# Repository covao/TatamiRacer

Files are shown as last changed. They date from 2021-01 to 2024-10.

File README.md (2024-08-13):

[Japanese](https://github.com/covao/TatamiRacer/blob/master/README_JP.md) / [English](https://github.com/covao/TatamiRacer/blob/master/README.md)  

TatamiRacerLogo
### ver 2.0      
TatamiRacer is a tiny autonomous driving car based on the ["TAMIYA MINI 4WD" kit](https://www.tamiya.com/english/mini4wd/m4item/m4item.htm). It can operate within the space of a single ["Tatami"](https://en.wikipedia.org/wiki/Tatami) mat, approximately 1.8m x 0.9m. The car uses ["Donkey Car"](http://docs.donkeycar.com/) software for deep learning and self-driving control. Interestingly, the Japanese word "Tatami" also brings to mind convolution operations in neural networks.

### YouTube  
- TatamiRacer 

(https://www.youtube.com/watch?v=b-pkVy8e3DA)  

- TatamiRacer at Maker Faire Tokyo 2022  

(https://www.youtube.com/watch?v=s3ll8Y1OPn8)  

# Release History

### [ver 1.0](https://github.com/covao/TatamiRacer/tree/1.0) 2023-05-28
### [ver 2.0](https://github.com/covao/TatamiRacer)
- Renewed 3D Parts
- Reduced mobile battery size and weight
- Supports installation of Raspberry Pi Zero 2

# Bills of Materials(BOM)
| Parts Name | Remarks |Minimum Configuration|Recommend Configuration|Amazon-JP|Amazon-US|
|:---|:---|:---:|:---:|:---:|:---:|
| Raspberry Pi Zero2 W ||+|| [Link](https://www.amazon.co.jp/dp/B09LH5SBPS/) | [Link](https://www.amazon.com/dp/B09LH5SBPS) |
| Raspberry Pi 4 |Select 2,4 or 8GB RAM||+| [Link](https://www.amazon.co.jp/dp/B09GRVDPCX/) | [Link](https://www.amazon.com/dp/B07TC2BK1X) |
| Raspberry Pi Camera Module  | v1.3:OV5647(Omnivision) or v2.1:IMX219Pq3(SONY)|+|+| [v1.3](https://www.amazon.co.jp/dp/B073RCXGQS/), [v2.1](https://www.amazon.co.jp/dp/B01F1SWTZE)| [v1.3](https://www.amazon.com/dp/B07QNSJ32M/),  [v2.1](https://www.amazon.com/dp/B01ER2SKFS)|
| Micro SD Card | 16GB or more|+|+| [e.g. SanDisk](https://www.amazon.co.jp/dp/B0CH2WM7QY/) | [e.g. SanDisk](https://www.amazon.com/dp//B08J4HJ98L) |
| Mobile Battery | Size:53x85x9.0mm Voltage:5V Current:Up to 2.1A |+|+|[Meisei C0303](https://www.amazon.co.jp/dp/B07Q5M3CLQ/) | [Atom Tech Super Slim Power Bank](https://www.amazon.com/dp/B07JZCZSH9/) |
| Motor Driver Module| For DC Motor/H-Bridge|+|+| [L298N ](https://www.amazon.co.jp/dp/B083DT2DMV/) |[L298N ](https://www.amazon.com/dp/B07Y1QJZK3/) |
| Pin Headder | Male 90deg / For Motor Dirver|+|+| [Link](https://www.amazon.co.jp/dp/B00V4V703O/) |[Link](https://www.amazon.com/dp/B0979568B3/) |
| 130 DC Motor | Low Speed (<8000 RPM) and Low Current(<500mA)|+|+|[TAMIYA](https://www.amazon.co.jp/dp/B005AFBLIA/),[uxcell](https://www.amazon.co.jp/dp/B07CWLWRYJ/) | [uxcell](https://www.amazon.com/dp/B01ERLPVJW) |
| Micro Servo |TowerPro SG90(0.1sec/60deg)|+|+| [Link](https://www.amazon.co.jp/dp/B016FKJJ8M/) | [Link](https://www.amazon.com/dp/B07MLR1498/) |
| TAMIYA Mini 4WD Kit |VZ Chassis and Your Favorite Body. Select Gear Rate 3.5:1 or 5:1 (Recommend 5:1 Gear )|+|+| [Elephant with 5:1 gear](https://www.amazon.co.jp/dp/B08VX3W3Q6/), [TOYOTA Yaris with 3.5:1 Gear](https://www.amazon.co.jp/dp/B08C5FM9HM/), [Honda e with 3.5.1 Gear](https://www.amazon.co.jp/dp/B08HK7HWCM/), [Dual Ridge Jr](https://www.amazon.co.jp/dp/B088FK3NC2/) | [Elephant with 5:1 gear](https://www.amazon.com/dp/B08VX3W3Q6/), [TOYOTA Yaris with 3.5:1 Gear](https://www.amazon.com/dp/B08C5FM9HM/), [Honda e with 3.5.1 Gear](https://www.amazon.com/dp/B08HK7HWCM/), [Dual Ridge Jr](https://www.amazon.com/dp/B088FK3NC2/) |
|TAMIYA Gear Set |If you change gear rate (e.g. 5:1)|||[15516](https://www.amazon.co.jp/dp/B0043RN7W4/)|[15516](https://www.amazon.com/dp/B0043RN7W4/)|
| TAMIYA Mini 4WD Roller parts | Need Spacer and M2x10 screws|+|+| [15381](https://www.amazon.co.jp/dp/B001E40PXI/), [95391](https://www.amazon.co.jp/dp/B07F8RLJBQ/),[15435](https://www.amazon.co.jp/dp/B005GJCC9C/)|[15435](https://www.amazon.com/dp/B005GJCC9C/) | 
| M2x15 or M2x16 mm bolt | For front wheel shaft |+|+| [15508](https://www.amazon.co.jp/dp/B01MXVKDOM/),  [15233](https://www.amazon.co.jp/dp/B001VZE9MS/)| [Link](https://www.amazon.com/dp/B07YS5ZSZH/) |
| TAMIYA MINI4WD 72mm Shaft | For Extended Rear Shaft|+|+| [Link](https://www.amazon.co.jp/dp/B003GALRS0/) | [Link](https://www.amazon.com/dp/B002CAO2IC/) |
| Jumper Cable | Female connector to Female connector 10cm|+|+| [Link](https://www.amazon.co.jp/dp/B07MR1SVVR/) | [Link](https://www.amazon.com/dp/B0742RS6YL) |
| Type-C USB Cable(L Headder) | Short cable 15-20cm ||+| [e.g. aceyoon](https://www.amazon.co.jp/dp/B0B4JQ41SW/)| [e.g. aceyoon](https://www.amazon.com/dp/B096VYVR17/) |
| Gamepad | USB or Bluetooth | |+| [F710](https://www.amazon.co.jp/dp/B00CDG7994/), [PS4 Compatible Gamepad](https://www.amazon.co.jp/dp/B0C4NW3G8J/)  | [F710](https://www.amazon.com/dp/B0041RR0TW/), [PS4 Compatible Gamepad](https://www.amazon.com/dp/B0C4NW3G8J/) |
||  || |  |  |
| Approximate cost (without Raspberry Pi and micro SD card) |  |6,000 yen |10,000 yen |  |  |

# 3D Printed Parts

## Assembly
See [3D Viewer](3d/tatamiracer_assembly.stl)  
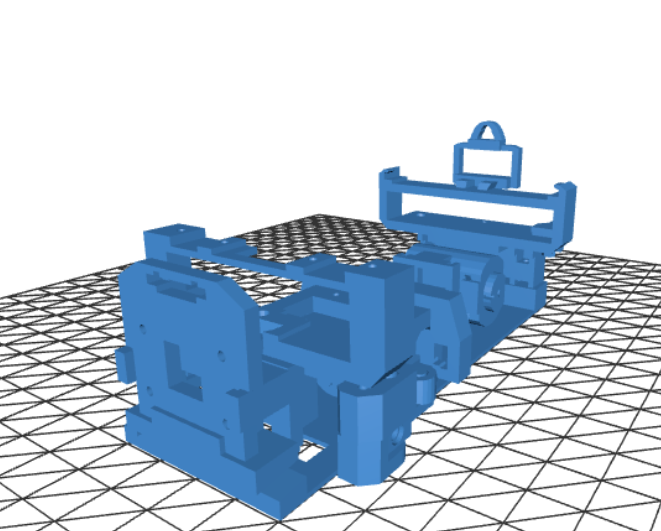
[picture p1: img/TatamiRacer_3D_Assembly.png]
  
  
## Kit for 3D print
See [3D Viewer](3d/tatamiracer_kit.stl)  
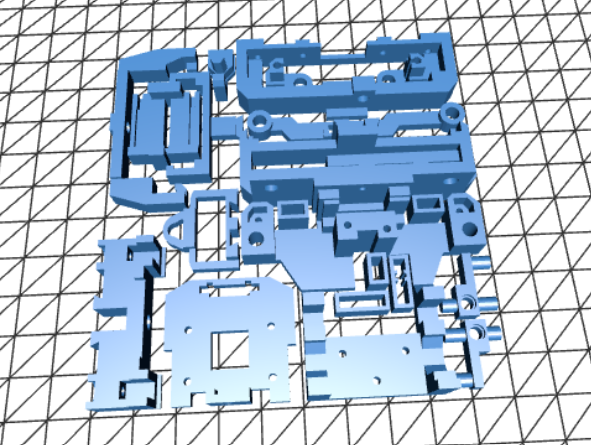
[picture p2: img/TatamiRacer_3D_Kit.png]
  
  
# Circuit Diagram
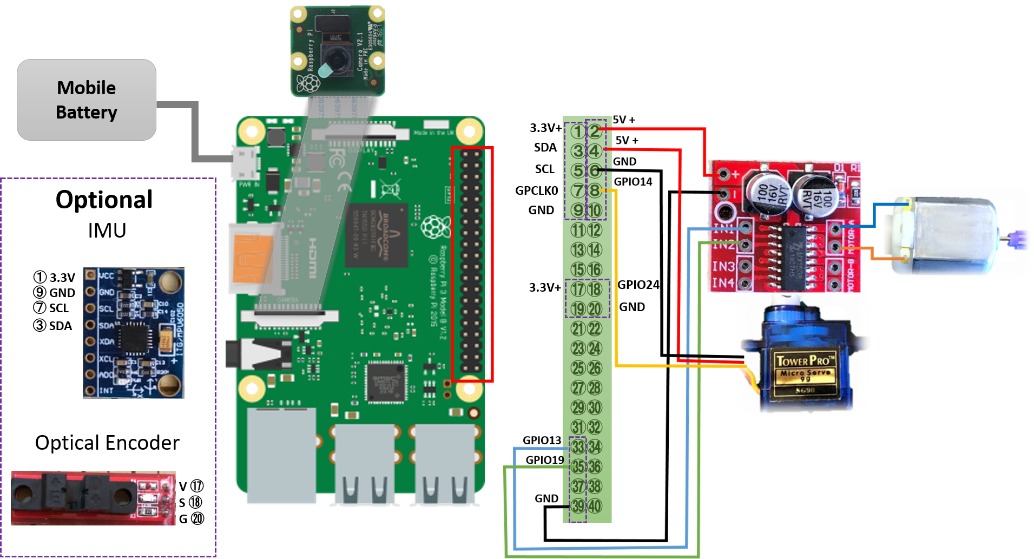
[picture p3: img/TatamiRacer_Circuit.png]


# Body
Various type of Mini-4WD body can be attaced .e.g. [Amazon JP](https://www.amazon.co.jp/s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), [Amazon US](https://www.amazon.com/s?k=tamiya+1%2F32+mini4wd&ref=nb_sb_noss)  
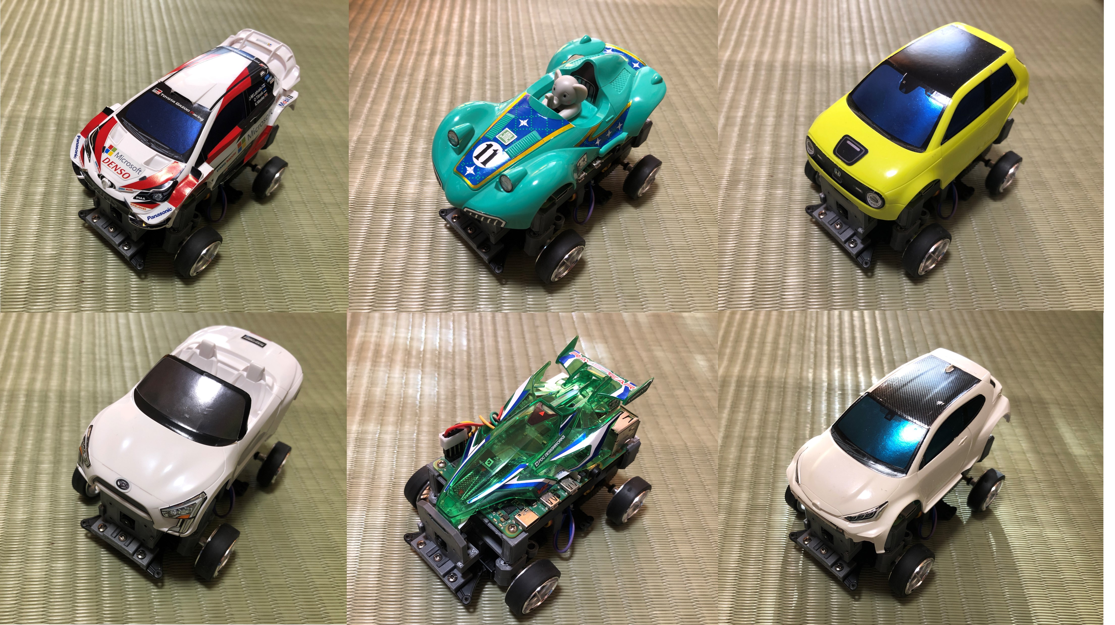
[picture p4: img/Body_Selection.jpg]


# Tatami-Circuit Cource
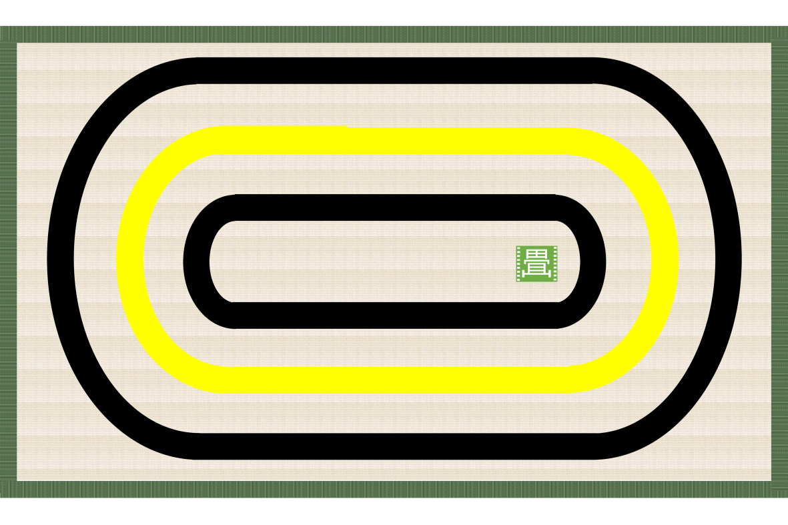
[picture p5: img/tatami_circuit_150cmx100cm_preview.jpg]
  

## Image data for printed fabric 
Fabric print service available  
- [Tatami-Circuit 150cmx100cm 200dpi](img/tatami_circuit_150cmx100cm_200dpi.jpg)  
- [Tatami-Circuit 110cmx100cm 200dpi](img/tatami_circuit_110cmx100cm_200dpi.jpg)  

# [TatamiRacer Assembly Instructions](doc/Assembly_Instructions.md)
See [TatamiRacer Assembly Instructions](doc/Assembly_Instructions.md)  
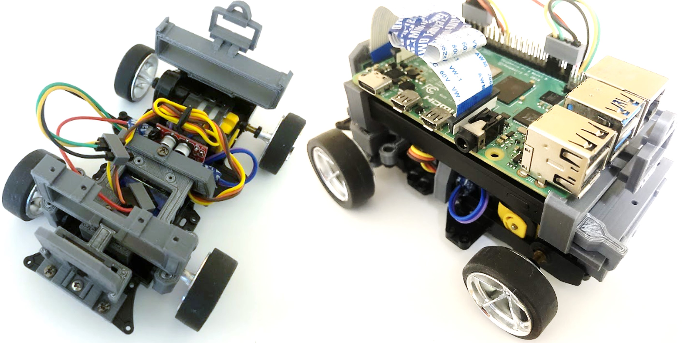
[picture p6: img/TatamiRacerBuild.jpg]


# [How to Setup Software](doc/HowToSetupSoftware.md) 
See [How To Setup Software](doc/HowToSetupSoftware.md)  
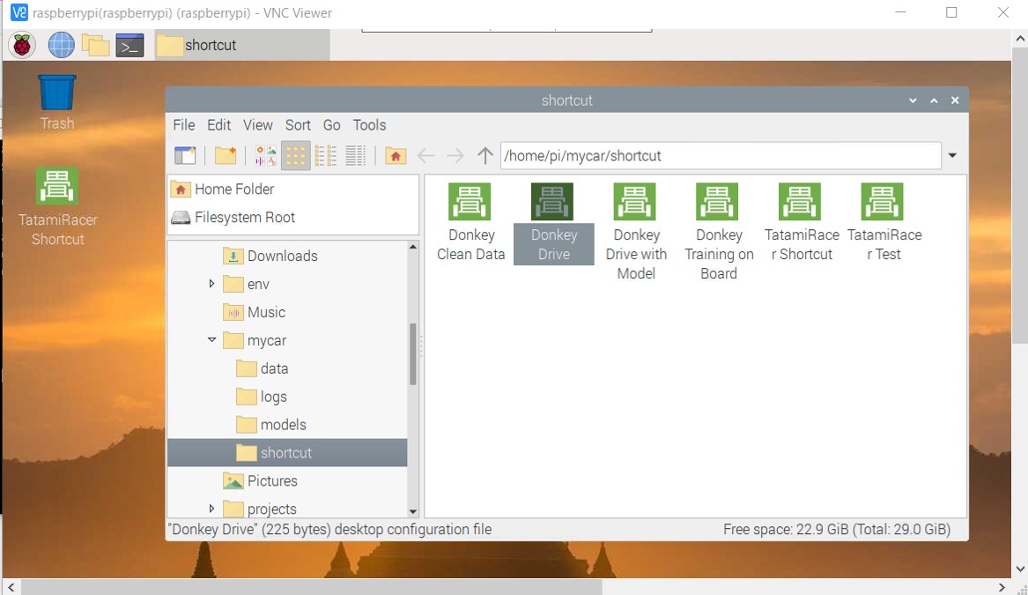
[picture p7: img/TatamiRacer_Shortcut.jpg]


#  [How to Calibrate TatamiRacer](doc/HowToCalibrateTatamiRacer.md)  
See [How to Calibrate TatamiRacer](doc/HowToCalibrateTatamiRacer.md)  
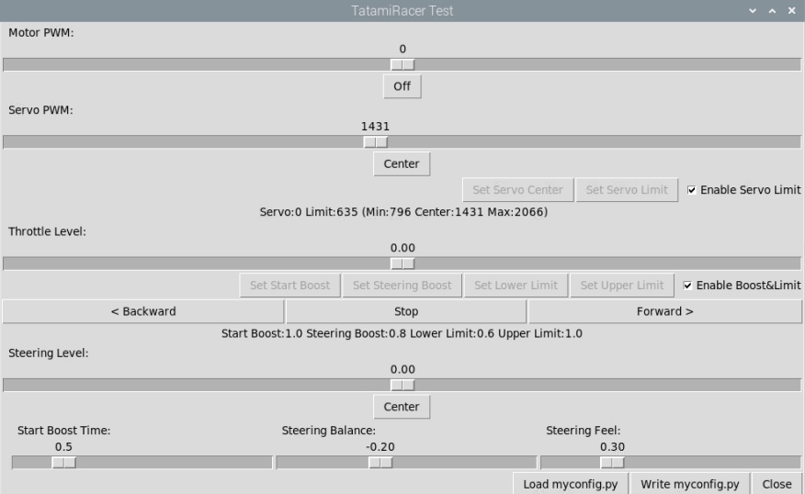
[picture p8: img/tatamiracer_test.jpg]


# [How to Get Driving](doc/HowToGetDriving.md)
See [How to Get Driving](doc/HowToGetDriving.md)  
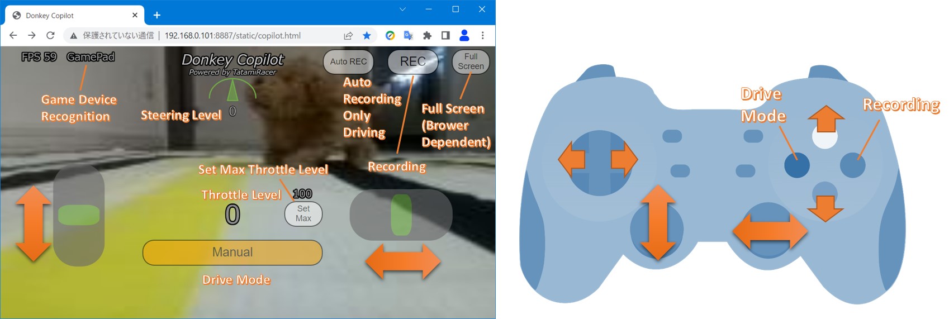
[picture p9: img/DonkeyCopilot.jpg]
  

Click to see the UI operation screen  
[Donkey Copilot Broweser Demo](https://covao.github.io/DonkeyCopilot/copilot.html?demo)

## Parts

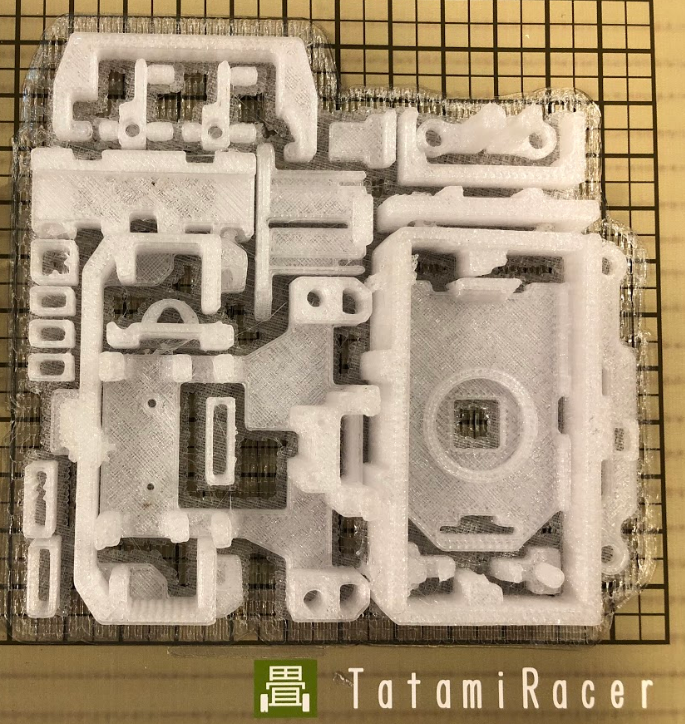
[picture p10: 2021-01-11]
img/printed_parts.png

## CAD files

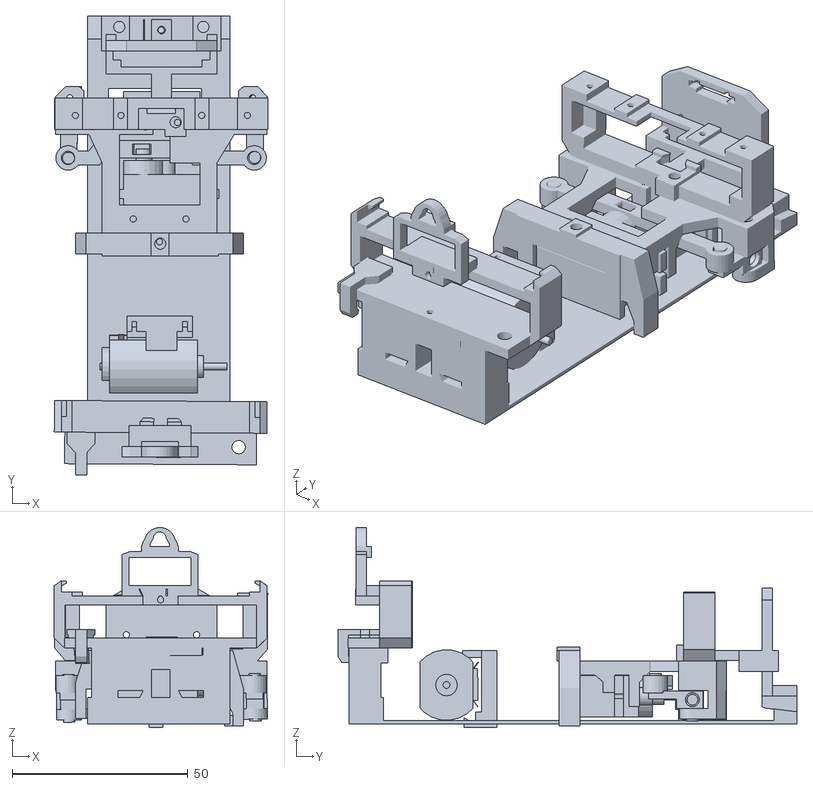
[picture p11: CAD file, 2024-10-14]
3d/tatamiracer_assembly.stl
60.8 x 130.7 x 57.0

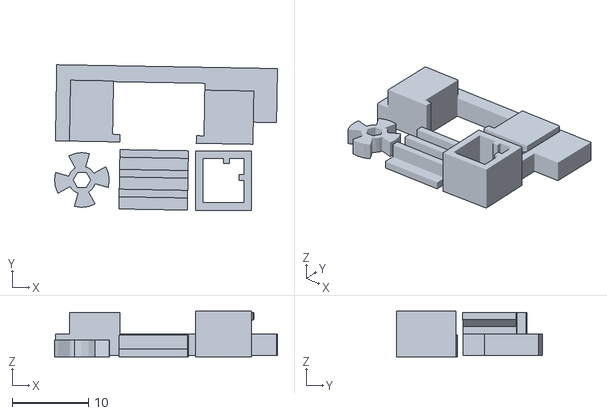
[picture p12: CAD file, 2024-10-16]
3d/tatamiracer_encoder_kit.stl
29.3 x 19.1 x 6.00

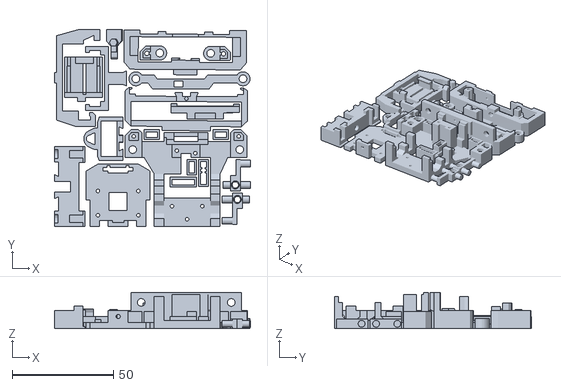
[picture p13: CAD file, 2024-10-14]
3d/tatamiracer_kit.stl
97.0 x 97.3 x 18.0

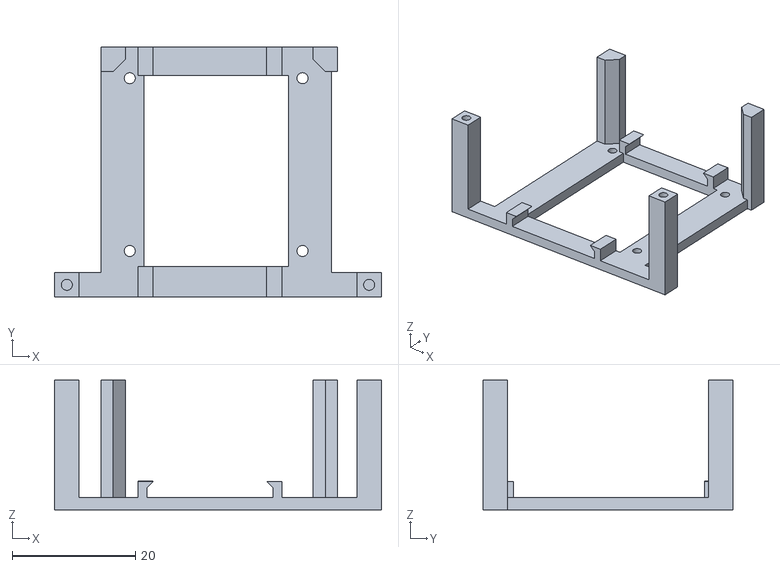
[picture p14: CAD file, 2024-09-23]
3d/lidar_mount_kit.stl
53.0 x 40.6 x 21.0

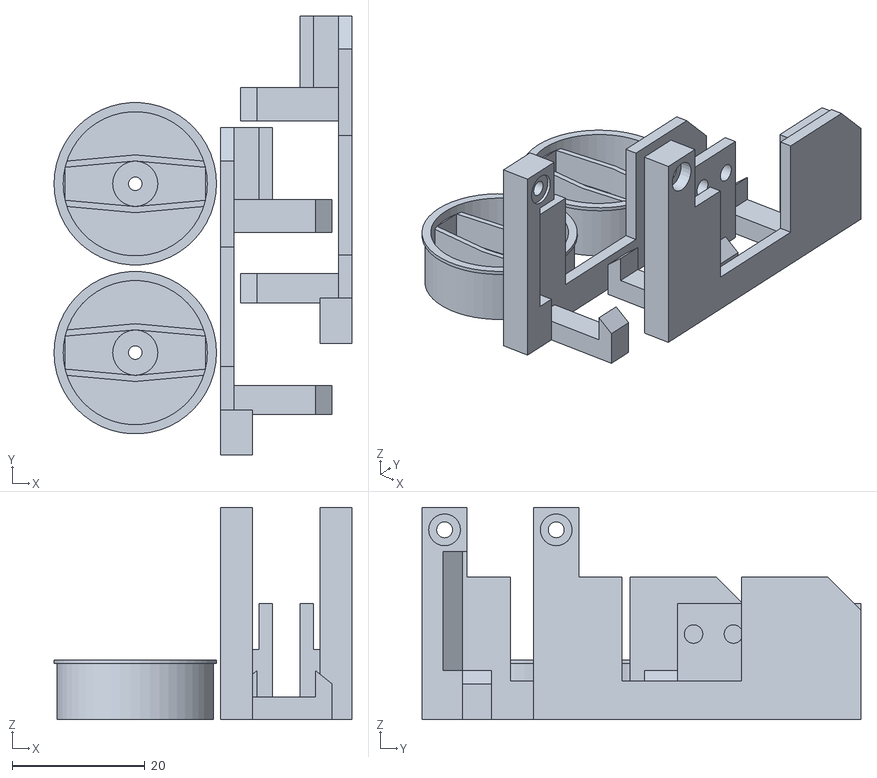
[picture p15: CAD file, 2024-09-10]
3d/differential_wheel_kit.stl
44.9 x 66.1 x 32.0

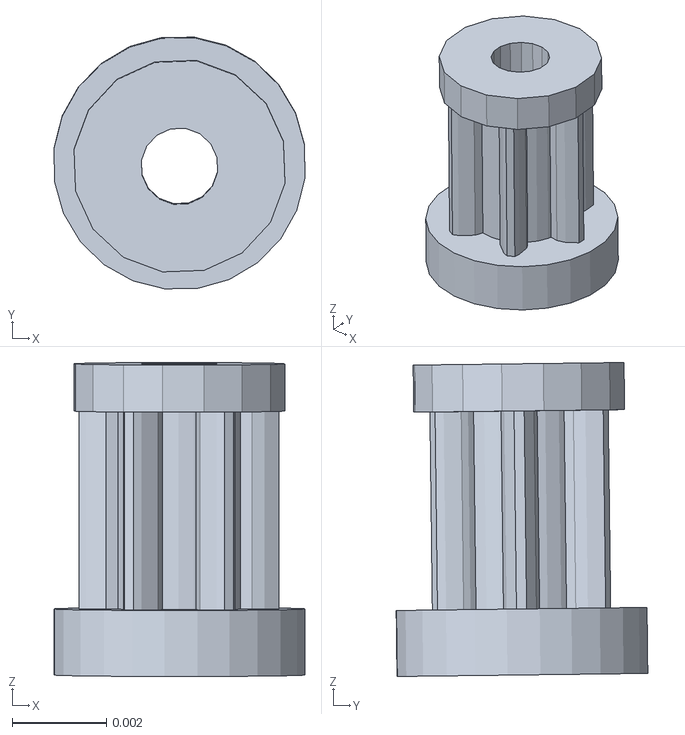
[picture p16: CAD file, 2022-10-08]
3d/pinion_gear_6t.stl
0.00532 x 0.00534 x 0.00666

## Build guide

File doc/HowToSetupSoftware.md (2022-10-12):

[Japanese(Google Translate)](https://github-com.translate.goog/covao/TatamiRacer/blob/master/doc/HowToSetupSoftware.md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)  

# How To Setup Software

TatamiRacer can use DonkeyCar software.  
This page describes about installing DonkeyCar software and custumizing TatamiRacer.  

# Install Raspberry Pi OS using Raspberry Pi Imager
1. Download "Raspberry Pi Imager" from [Raspberry Pi official site](https://www.raspberrypi.org/software/). 
2. Install "Raspberry Pi Imager".
3. Start "Raspberry Pi imager".
4. Downlowd Raspbian-OS file from the following site.    
For TatamiRacer it is recommended to install the desktop version.  
Stable Raspbian version for DonkeyCar 
https://downloads.raspberrypi.org/raspios_armhf/images/raspios_armhf-2021-05-28/  
	2021-05-07-raspios-buster-armhf.zip     
 See note of Raspbian Bullseye issue of Donkey Car.
 [Flash Operating System](https://docs.donkeycar.com/guide/robot_sbc/setup_raspberry_pi/#step-1-flash-operating-system)

5. If you press advanced configration button, you can set WIFI, host name, SSH, user name and password, local setting.
6. Write Raspbian OS to your micro SD card.
7. Un plugging and re-inserting micro SD card.
8. Check the SD card drive. Boot files are appeared if OS image was flashed successfuly.

# Setup the WiFi for Raspberry Pi
Internet connection on Raspberry Pi is required before installation.
## - Method 1: WiFi setting in the Raspberry Pi Desktop (Monitor and keyboard for Raspberry pi are required.)
1. Insert micro SD card into Raspi.
2. Plug USB power supply of Raspi.
3. Login Raspberry Pi Desktop
4. Set Wifi configuration from Raspberry pi Desktop  
 See [Wireless connectivity in the Raspberry Pi Desktop](https://bwww.raspberrypi.org/documentation/configuration/wireless/desktop.md)
## - Method 2: WiFi setting by boot configuration file (Remote access is available without Raspi monitor and keyboard.) 
1. Create wpa_supplicant.conf in the top of SD card then edit ssid and password by texteditor  
 Please see ["Setting up a Raspberry Pi headless"](https://docs.donkeycar.com/guide/robot_sbc/setup_raspberry_pi/)
2. Create ssh file (empty file) in the top of SD card to enable SSH.  
 Please see ["SSH (Secure Shell)>3. Enable SSH on a headless Raspberry Pi"](https://www.raspberrypi.org/documentation/remote-access/ssh/)
3. Insert micro SD card into Raspi.
4. Plug USB power supply of Raspi and wait few minutes.
5. Launch command prompt and enter following command.  
 Check network connection between host pc and raspberry pi.  
~~~
 ping raspberrypi
 
~~~
OR
~~~
 ping raspberrypi.local
 
~~~

6. Launch ssh by following command.  
~~~
ssh-keygen -R raspberrypi
ssh pi@raspberrypi

~~~
If <code>"The authenticity of host 'raspberrypi... Are you sure you want to continue connecting (yes/no)?"</code> is appeared, enter yes.  

7. Enter password. Initial Password:<code>raspberry</code>

# Setup VNC
Remote desktop environment is useful to access Raspberry pi from host pc.  
1. You can install VNC with the following command.  
(You can enter the command from remote ssh or Raspberry pi desktop ternminal.)  
~~~
yes | sudo apt-get update
yes | sudo apt install realvnc-vnc-server realvnc-vnc-viewer
yes | sudo raspi-config nonint do_vnc 0

~~~
2. Set screen resolution
Select "Display Options-> Resolution" (At least 1280 x 720 recommended.)
~~~
sudo raspi-config

~~~
3. Select exit and reboot.  

4. Installation on the host PC is also requreired.  
See ["VNC (Virtual Network Computing)"](https://www.raspberrypi.org/documentation/remote-access/vnc/).  

# Launch Raspberry Pi Desktop
If you have VNC installed, you can use Remote Desktop.
1. Start Raspberry Pi Desktop.  
2. Launch Terminal window.

# Install Donkey Car Application for Raspberry Pi
## Method 1: Install by Shell Script 
1. First execute the following command.  
~~~
yes | sudo apt-get update
yes | sudo apt-get upgrade

~~~
*Press q when you see the following message.
<code>if webkit2gtk (2.31.1-1) experimental; urgency=medium ...</code>

2. The following command will install the latest Donkey Car application and create default "mycar" application.
~~~
wget "https://raw.githubusercontent.com/covao/TatamiRacer/master/raspi/install/install_donkey_raspi.sh" -O "install_donkey_raspi.sh"
sh -x install_donkey_raspi.sh

~~~
The shell script is here. [install_donkey_raspi.sh](https://raw.githubusercontent.com/covao/TatamiRacer/master/raspi/install/install_donkey_raspi.sh)

## Method 2: Install Manually Step by Step
See following procedure.
- [Get Your Raspberry Pi Working Step6 -Step12 ](https://docs.donkeycar.com/guide/robot_sbc/setup_raspberry_pi/#step-6-update-and-upgrade)
- [Create your car application](https://docs.donkeycar.com/guide/create_application/)

# Setup TatamiRacer by Shell Script 
The following command will replace 'manage.py' and 'config.py' and add 'tatamiracer_test.py' for TatamiRacer.  
In addition it will create the shortcut into desktop.  
~~~
wget "https://raw.githubusercontent.com/covao/TatamiRacer/master/raspi/install/setup_tatamiracer.sh" -O "setup_tatamiracer.sh"
sh -x setup_tatamiracer.sh

~~~
The shell script is here. [setup_tatamiracer.sh](https://raw.githubusercontent.com/covao/TatamiRacer/master/raspi/install/setup_tatamiracer.sh)



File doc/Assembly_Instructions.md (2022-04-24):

[Japanese(Google Translate)](https://github-com.translate.goog/covao/TatamiRacer/blob/master/doc/Assembly_Instructions.md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)  

# TatamiRacer Assembly Instructions 
### All Parts 
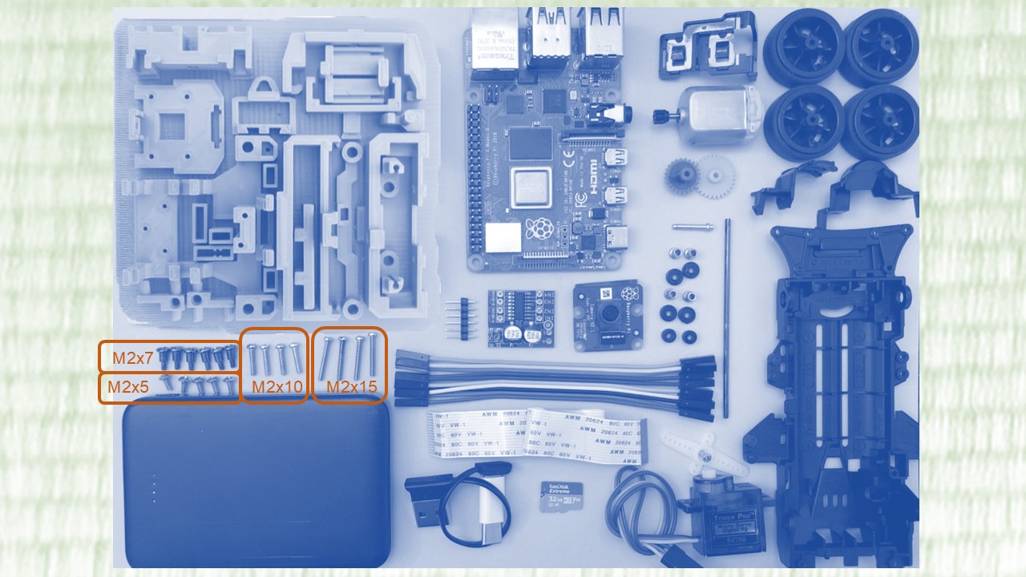
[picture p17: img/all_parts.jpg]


### Step 1. Assembling Front Wheel Parts
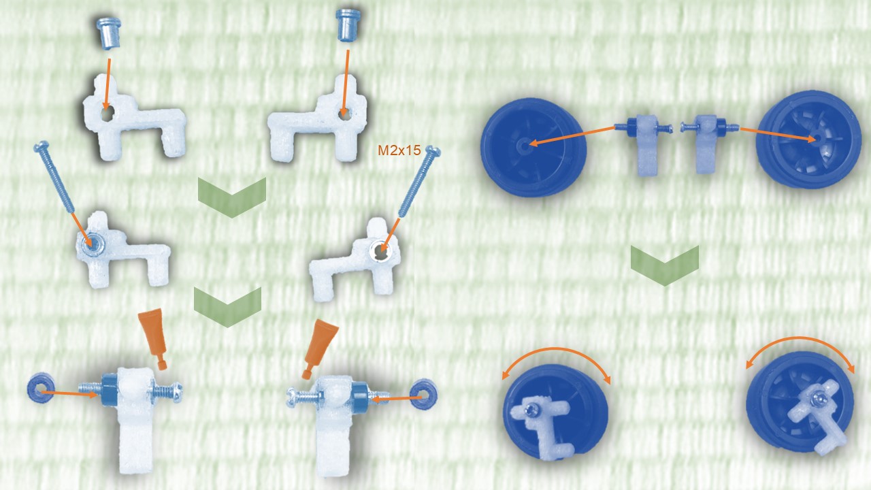
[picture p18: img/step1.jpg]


### Step 2. Assembling Front Steering Unit
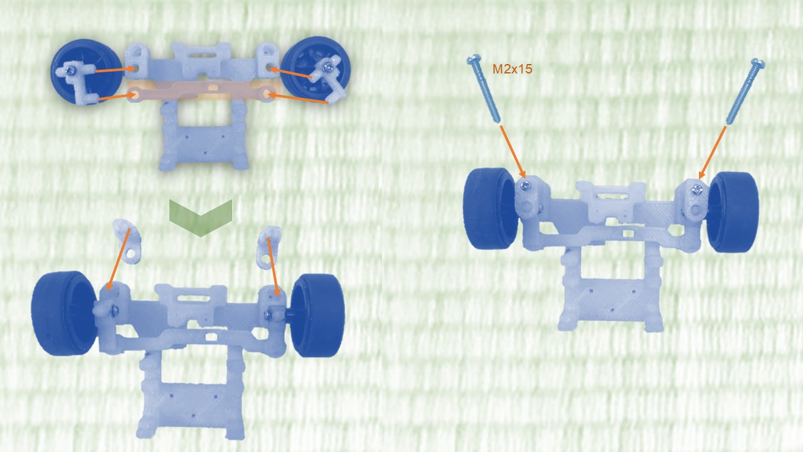
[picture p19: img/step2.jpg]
 

### Step 3. Assembling Servo Motor
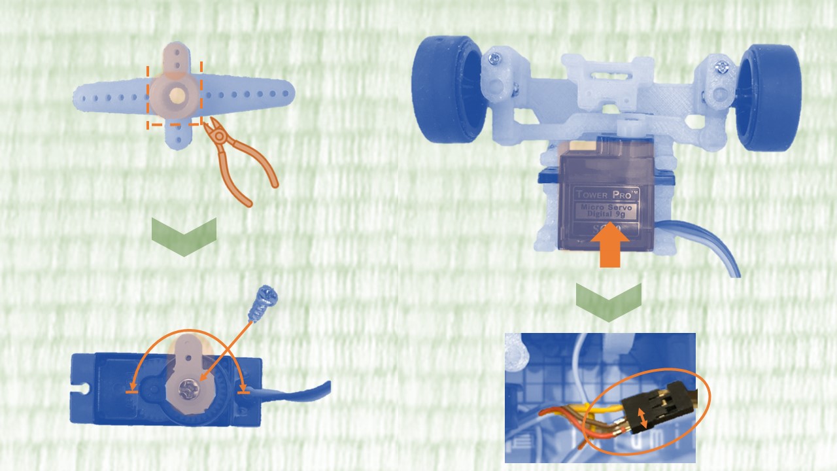
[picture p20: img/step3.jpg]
 

### Step 4. Mounting Front Steering Unit 
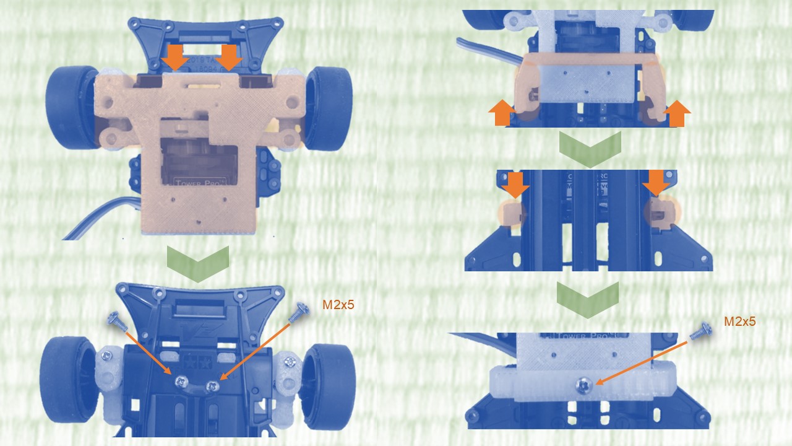
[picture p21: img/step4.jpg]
 

### Step 5. Assembling Rear Wheel Drive Unit
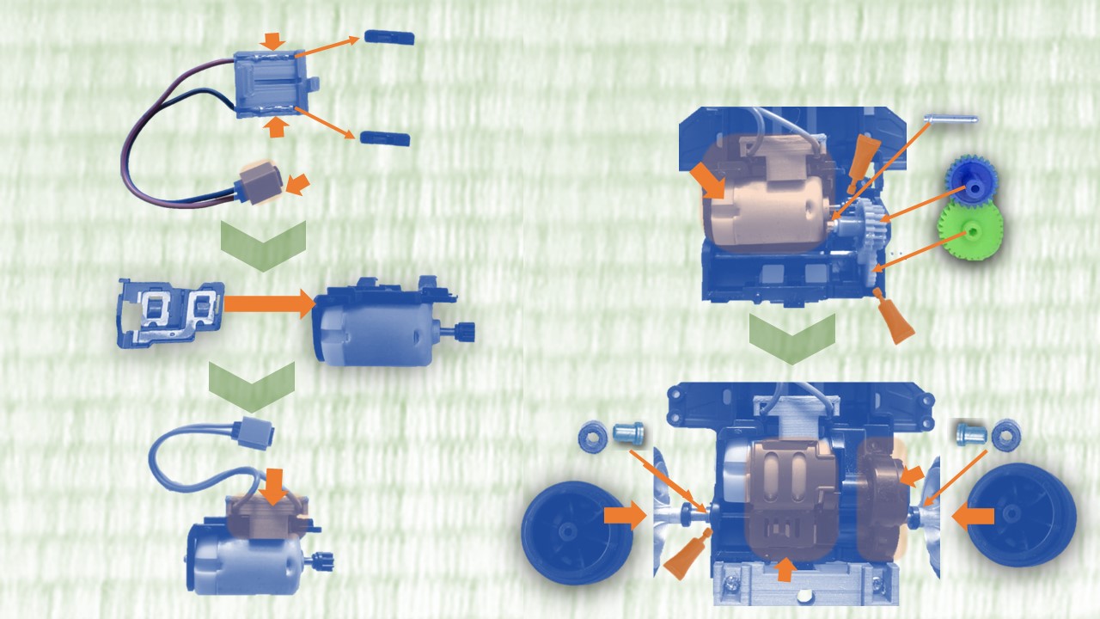
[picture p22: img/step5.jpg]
 

### Step 6. Fixing Mount Parts
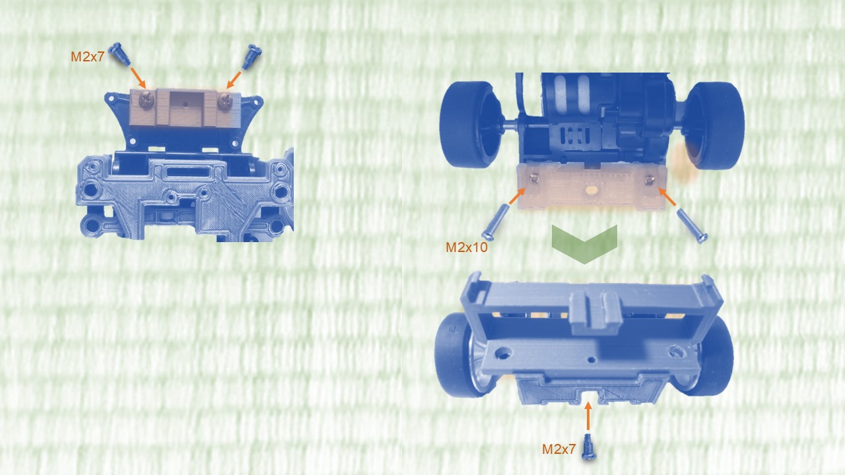
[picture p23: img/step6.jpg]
 

### Step 7. Assembling Camera Module 
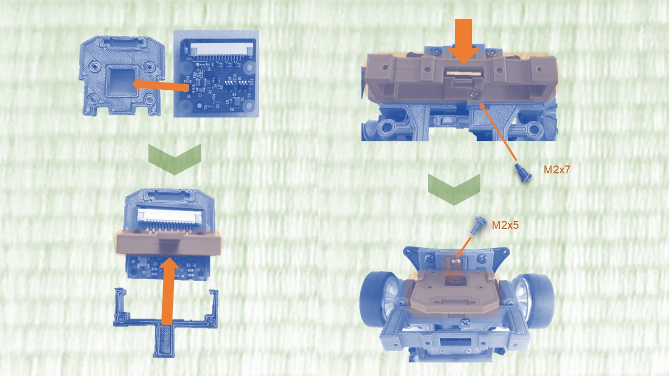
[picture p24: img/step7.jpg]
 

### Step 8. Making Motor Driver and Harness 
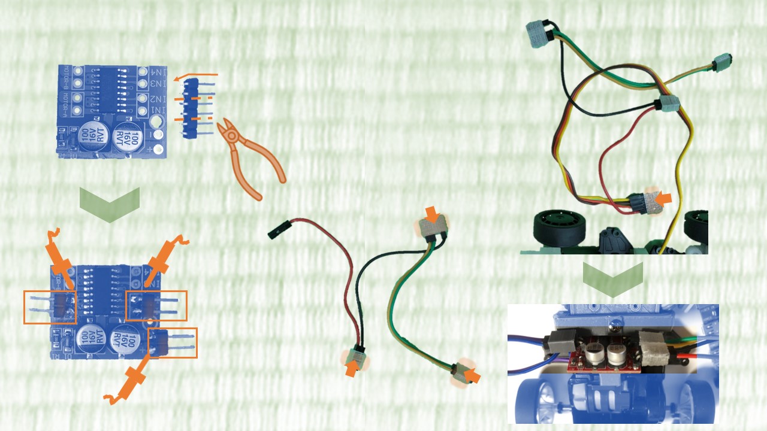
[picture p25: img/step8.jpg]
 

### Step 9. Attaching Raspberry PI Board and Battery
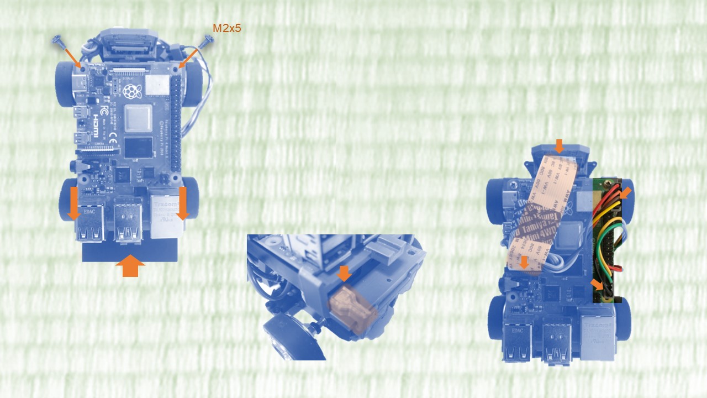
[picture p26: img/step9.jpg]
 

### Step 10. Attaching the body
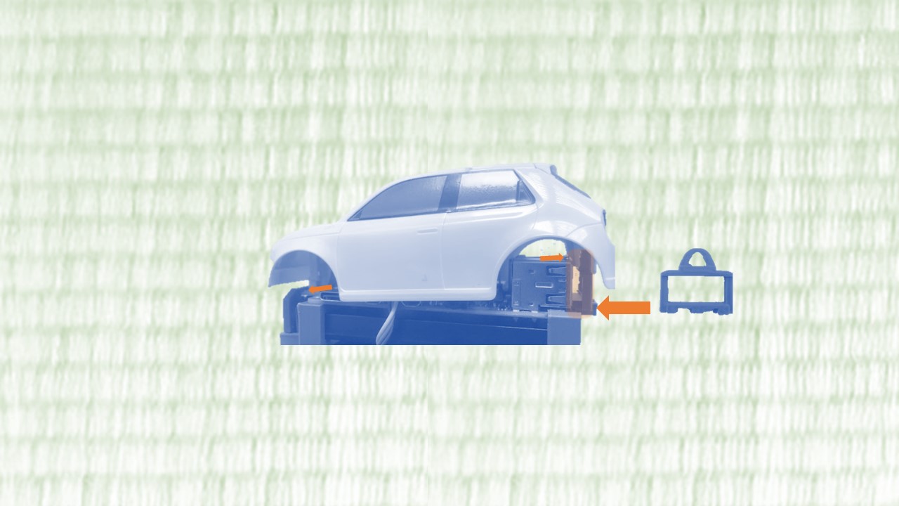
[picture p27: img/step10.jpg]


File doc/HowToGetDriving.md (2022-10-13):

[Japanese(Google Translate)](https://github-com.translate.goog/covao/TatamiRacer/blob/master/doc/HowToGetDriving.md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)
# How To Get Driving
TatamiRacer can be operated remotely with the web browser.  
This article is how to drive with a DonkeyCar web controller.  
See below for more information.
- [DonkeyCar > Drive your car](https://docs.donkeycar.com/guide/get_driving/)

## Start DonkeyCar Application
### Method 1: Desktop Shortcut 
1. Start "Donky Drive" or "Donky Drive with Model  


### Method 2: Command from terminal
1. Enter following command from terminal.
~~~
cd ~/mycar
python manage.py drive
~~~

## Web Controller
### Method 1: Donkey Copilot (Web controller suitable for smartphone)  

Please see https://github.com/covao/DonkeyCopilot

### [Demo Link](https://covao.github.io/DonkeyCopilot/copilot.html?demo)  

### Method 2: DonkeyCar web Controller  
2. Start the Web browser from the host PC or smart phone and enter following URL.
~~~
http://raspberrypi:8887/drive
~~~

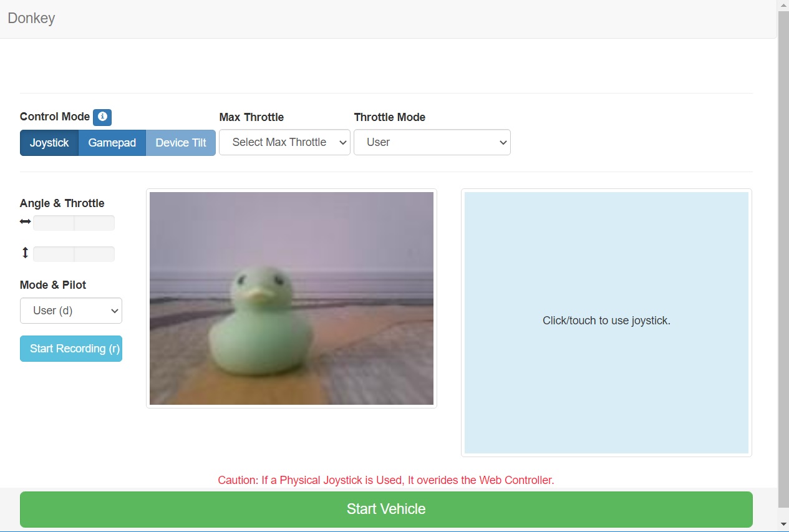
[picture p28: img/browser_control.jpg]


3.  Select Control Mode  
- **Joystick mode**   It can be control by touch screen.
- **Gemepad mode**  It can be controlled by the gamepad connected to the host PC.

4. Drive your car.

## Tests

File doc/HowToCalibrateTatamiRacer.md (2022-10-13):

[Japanese(Google Translate)](https://github-com.translate.goog/covao/TatamiRacer/blob/master/doc/HowToCalibrateTatamiRacer.md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) 

# How to Calibrate TatamiRacer

## Start TatamiRacaer Test Tool  
Launch "TatamiRacer Test" from shortcut or enter following command from terminal.
~~~
cd ~/mycar
python tatamiracer_test.py
~~~



## TatamiRacer Controller Overview
TatamiRacer controller enhance the motor start torque and feeling.  
This is a block diagram that controls throttle and steering.  
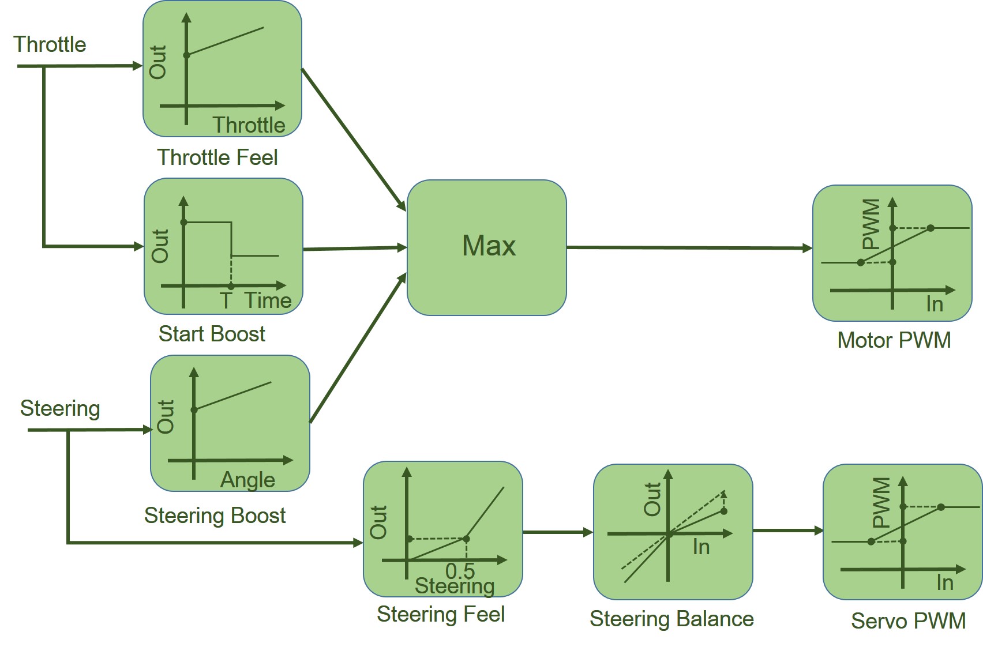
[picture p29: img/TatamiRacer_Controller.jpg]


## Basic Calibration
### Calibrate Servo PWM
Purpose: Adjust the position of the steering center and steering limit
1. Turn off the <code>"Enable Servo Limit"</code> check button.
2. Adjust center position by <code>"Servo PWM"</code> slider.
3. Click <code>"Set Servo Center"</code> push button.
4. Check running straight by <code>"Motor PWM"</code> slider.
5. Move <code>"servo PWM"</code> slider until steering stop.
7. Click <code>"Set Servo Limit"</code> push button.
8. Turn on <code>"Enable Servo Limit"</code> check button..
9. Check the steering limit.

### Write the parameters to the "myconfig.py" file
1. Click the <code>"Write myconfig.py"</code> button.
2. Press <code>"Yes"</code> button in the dialog.

## Advanced Calibration
### Calibrate the Throttle Start Boost
Purpose: Smooth acceleration by increasing the starting torque
1. Turn off the <code>"Enable Boost&Limit"</code> check button.
2. Set the throttle slider to Off.
3. Raise the throttle slider until the the car starts running.
4. Click <code>"Set Start Boost"</code> at the throttle level.   
5. Set the throttle slider to Off.
6. Turn on the <code>"Enable Boost&Limit"</code> check button.
7. Raise the throttle slider a little.
8. Check that the car starts running.
9. Adjust <code>"Start Boost Time"</code> for smooth acceleration.

### Calibrate the Throttle Feeling
Purpose: Improved throttle sensitivity
1. Turn off the <code>"Enable Boost&Limit"</code> check button.
2. Set the throttle slider to Off.
3. Raise the throttle slider until the car moves.
4. Reduce the throttle slider at the minimum value that the car keeps running.
5. Click <code>"Set Lower Limit"</code> at the throttle level.
6. If you want to reduce the maximum speed, set the <code>"Upper Limit"</code> less than 1.0.
7. Turn on the <code>"Enable Boost&Limit"</code> check button.
8. Raise the throttle slider a little.
9. Check that the car keeps running.

### Calibrate the Throttle Steering Boost
Purpose: Improved torque when cornering
1. Turn off the <code>"Enable Boost&Limit"</code> check button.
2. Set the throttle slider to Off.
3. Set the Steerling slide max.
4. Raise the throttle slider until the car moves.
5. Reduce the throttle slider at the minimum value that the car keeps running.
6. Click <code>"Set Steering Boost"</code> at the throttle level.
7. Turn on the <code>"Enable Boost&Limit"</code> check button.
8. Set the Steerling slide at center.
9. Raise the throttle slider a little.
10. Set the Steerling slide max (right side).
11. Check that the car keeps running.
12. Set the Steerling slide min (left side).
13. Check that the car keeps running.

### Calibrate the Steering Feeling
Purpose: Improved control of small steering angles
1. Adjust <code>"Steering Feel"</code> slider.
2. Move Steering slider from left to right.
3. Check the steering feeling.

### Calibrate the Steering Balance
Purpose: Make left and right turns the same level
1. Set <code>"Steering level"</code> to about -0.8. (left side)
2. Run the car and check turn level.
3. Set <code>"Steering level"</code> to about +0.8.(right side)
4. Check the balance and adjust <code>"Steering Balance"</code> level

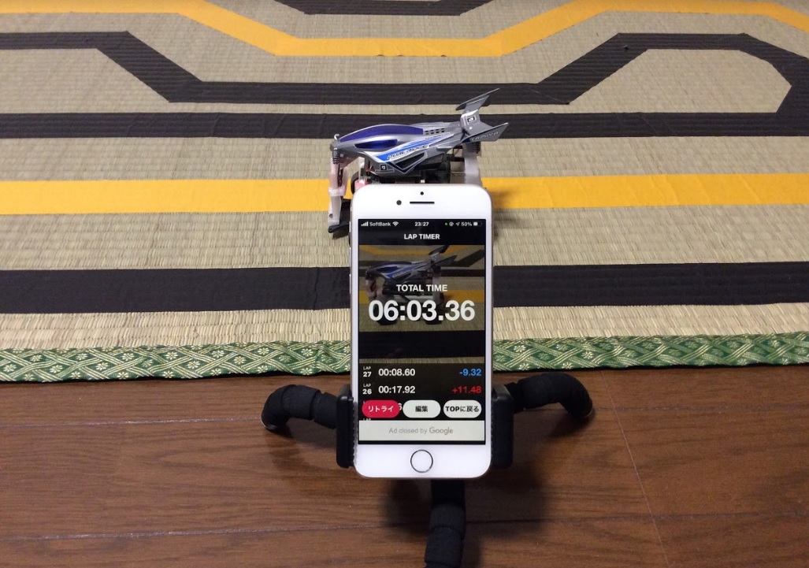
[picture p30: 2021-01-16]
img/LapTimeMeasurement.jpg

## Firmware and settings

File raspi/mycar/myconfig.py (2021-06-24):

# """ 
# My CAR CONFIG 

# This file is read by your car application's manage.py script to change the car
# performance

# If desired, all config overrides can be specified here. 
# The update operation will not touch this file.
# """

# import os
# 
# #PATHS
# CAR_PATH = PACKAGE_PATH = os.path.dirname(os.path.realpath(__file__))
# DATA_PATH = os.path.join(CAR_PATH, 'data')
# MODELS_PATH = os.path.join(CAR_PATH, 'models')
# 
# #VEHICLE
# DRIVE_LOOP_HZ = 20      # the vehicle loop will pause if faster than this speed.
# MAX_LOOPS = None        # the vehicle loop can abort after this many iterations, when given a positive integer.
# 
# #CAMERA
# CAMERA_TYPE = "PICAM"   # (PICAM|WEBCAM|CVCAM|CSIC|V4L|D435|MOCK|IMAGE_LIST)
# IMAGE_W = 160
# IMAGE_H = 120
# IMAGE_DEPTH = 3         # default RGB=3, make 1 for mono
# CAMERA_FRAMERATE = DRIVE_LOOP_HZ
CAMERA_VFLIP = True
CAMERA_HFLIP = True
# # For CSIC camera - If the camera is mounted in a rotated position, changing the below parameter will correct the output frame orientation
# CSIC_CAM_GSTREAMER_FLIP_PARM = 0 # (0 => none , 4 => Flip horizontally, 6 => Flip vertically)
# 
# # For IMAGE_LIST camera
# # PATH_MASK = "~/mycar/data/tub_1_20-03-12/*.jpg"
# 
# #9865, over rides only if needed, ie. TX2..
# PCA9685_I2C_ADDR = 0x40     #I2C address, use i2cdetect to validate this number
# PCA9685_I2C_BUSNUM = None   #None will auto detect, which is fine on the pi. But other platforms should specify the bus num.
# 
# #SSD1306_128_32
# USE_SSD1306_128_32 = False    # Enable the SSD_1306 OLED Display
# SSD1306_128_32_I2C_BUSNUM = 1 # I2C bus number
# 
# #DRIVETRAIN
# #These options specify which chasis and motor setup you are using. Most are using SERVO_ESC.
# #DC_STEER_THROTTLE uses HBridge pwm to control one steering dc motor, and one drive wheel motor
# #DC_TWO_WHEEL uses HBridge pwm to control two drive motors, one on the left, and one on the right.
# #SERVO_HBRIDGE_PWM use ServoBlaster to output pwm control from the PiZero directly to control steering, and HBridge for a drive motor.
# #PIGPIO_PWM uses Raspberrys internal PWM
DRIVE_TRAIN_TYPE = "PIGPIO_TATAMI" # SERVO_ESC|DC_STEER_THROTTLE|DC_TWO_WHEEL|DC_TWO_WHEEL_L298N|SERVO_HBRIDGE_PWM|PIGPIO_PWM|MM1|MOCK

#TatamiRacer Tunable Parameter (TATAMI_*)
TATAMI_STEERING_LEFT_PWM = 2172 #PWM value for full left steering (Center PWM + steering level)
TATAMI_STEERING_RIGHT_PWM = 916 #PWM value for full right steering
TATAMI_STEERING_FEEL = 0.3 #Steering Feeling Adjustment (Angle Level at Steering 50%)  
TATAMI_STEERING_BALANCE = -0.1 #Steering L/R Balance -1.0(L)..+1.0(R)
TATAMI_THROTTLE_START_BOOST_TIME = 0.9 #Throttle boost time[sec]
TATAMI_THROTTLE_START_BOOST = 1.0 #Throttle boost level for start torque up(0..1)
TATAMI_THROTTLE_UPPER_LIMIT = 1.0 #Throttle upper limit (0..1)
TATAMI_THROTTLE_LOWER_LIMIT = 0.8 #Throttle lower limit (0..1)
TATAMI_THROTTLE_STEERING_BOOST = 1.0 #Throttle boost adjustment by steering angle (0..1)

# 
# #STEERING
# STEERING_CHANNEL = 1            #channel on the 9685 pwm board 0-15
# STEERING_LEFT_PWM = 460         #pwm value for full left steering
# STEERING_RIGHT_PWM = 290        #pwm value for full right steering
 
# #STEERING FOR PIGPIO_PWM
# STEERING_PWM_PIN = 13           #Pin numbering according to Broadcom numbers
# STEERING_PWM_FREQ = 50          #Frequency for PWM
# STEERING_PWM_INVERTED = False   #If PWM needs to be inverted
# 
# #THROTTLE
# THROTTLE_CHANNEL = 0            #channel on the 9685 pwm board 0-15
# THROTTLE_FORWARD_PWM = 500      #pwm value for max forward throttle
# THROTTLE_STOPPED_PWM = 370      #pwm value for no movement
# THROTTLE_REVERSE_PWM = 220      #pwm value for max reverse throttle
# 
# #THROTTLE FOR PIGPIO_PWM
# THROTTLE_PWM_PIN = 18           #Pin numbering according to Broadcom numbers
# THROTTLE_PWM_FREQ = 50          #Frequency for PWM
# THROTTLE_PWM_INVERTED = False   #If PWM needs to be inverted
# 
# #DC_STEER_THROTTLE with one motor as steering, one as drive
# #these GPIO pinouts are only used for the DRIVE_TRAIN_TYPE=DC_STEER_THROTTLE
# HBRIDGE_PIN_LEFT = 18
# HBRIDGE_PIN_RIGHT = 16
# HBRIDGE_PIN_FWD = 15
# HBRIDGE_PIN_BWD = 13
# 
# #DC_TWO_WHEEL - with two wheels as drive, left and right.
# #these GPIO pinouts are only used for the DRIVE_TRAIN_TYPE=DC_TWO_WHEEL
# HBRIDGE_PIN_LEFT_FWD = 18
# HBRIDGE_PIN_LEFT_BWD = 16
# HBRIDGE_PIN_RIGHT_FWD = 15
# HBRIDGE_PIN_RIGHT_BWD = 13
# 
# 
# #ODOMETRY
# HAVE_ODOM = False                   # Do you have an odometer/encoder
# ENCODER_TYPE = 'GPIO'            # What kind of encoder? GPIO|Arduino|Astar
# MM_PER_TICK = 12.7625               # How much travel with a single tick, in mm. Roll you car a meter and divide total ticks measured by 1,000
# ODOM_PIN = 13                        # if using GPIO, which GPIO board mode pin to use as input
# ODOM_DEBUG = False                  # Write out values on vel and distance as it runs
# 
# # #LIDAR
# USE_LIDAR = False
# LIDAR_TYPE = 'RP' #(RP|YD)
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

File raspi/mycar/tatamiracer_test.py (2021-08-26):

# TatamiRacer Test for Steering Servo and Motor

import pigpio
import tkinter as tk
from tkinter import messagebox
import numpy as np
import os
import re
import time
import threading

pi = pigpio.pi()
gpio_pin0 = 13 #Motor1
gpio_pin1 = 19 #Motor2
gpio_pin2 = 14 #Servo
fname = os.getcwd()+r'/myconfig.py' #for Donkey Car parameter file

#Variable
class cfg: #parameter
    pass
root = tk.Tk()
motor = tk.IntVar()
servo = tk.IntVar()
servo_center = tk.IntVar()
servo_limit = tk.IntVar()
servo_limit_flag = tk.BooleanVar()
throttle_boost_enable_flag = tk.BooleanVar()
throttle = tk.DoubleVar()
steering = tk.DoubleVar()

throttle_start_boost = tk.DoubleVar()
throttle_start_boost_time = tk.DoubleVar()
throttle_upper_limit = tk.DoubleVar()
throttle_lower_limit = tk.DoubleVar()
throttle_steering_boost = tk.DoubleVar()
steering_feel = tk.DoubleVar()
steering_balance = tk.DoubleVar()

throttle_start_boost_time0 = 0.0
throttle_start_boost_val = 0.0
throttle_deadzone=0.01

timer_enable = True
def timer100ms():
    global throttle_start_boost_val,throttle_start_boost_time0
    if not timer_enable:
        return

    throttle_abs = np.abs(throttle.get())
    t_current = time.time()
    if throttle_abs<=throttle_deadzone:
        throttle_start_boost_time0 = t_current
    #Throttle Boost
    t = t_current-throttle_start_boost_time0
    if(t <= throttle_start_boost_time.get()):
        throttle_start_boost_val = throttle_start_boost.get() #Boost mode
    else:
        throttle_start_boost_val = 0.0
        set_throttle(0)

    t = threading.Timer(0.1, timer100ms)
    t.start()

def set_timer():
    t = threading.Thread(target=timer100ms)
    t.start()
    return t
 
def set_config():
    servo_max= cfg.TATAMI_STEERING_LEFT_PWM
    servo_min= cfg.TATAMI_STEERING_RIGHT_PWM
    tmp=int(servo_max-servo_min)/2
    servo_limit.set(tmp)
    servo_limit_flag.set(True)
    throttle_boost_enable_flag.set(True)
    servo_center.set(servo_min+tmp)
    servo.set(servo_center.get())
    motor.set(0)
    throttle.set(0)
    steering.set(0)
    set_motor(0)
    set_servo(0)

    steering_feel.set(cfg.TATAMI_STEERING_FEEL)
    steering_balance.set(cfg.TATAMI_STEERING_BALANCE)
    throttle_start_boost_time.set(cfg.TATAMI_THROTTLE_START_BOOST_TIME)
    throttle_start_boost.set(cfg.TATAMI_THROTTLE_START_BOOST)
    throttle_upper_limit.set(cfg.TATAMI_THROTTLE_UPPER_LIMIT)
    throttle_lower_limit.set(cfg.TATAMI_THROTTLE_LOWER_LIMIT)
    throttle_steering_boost.set(cfg.TATAMI_THROTTLE_STEERING_BOOST)
    status()
    status2()
    disable_button()

def load_config():
    f=open(fname)
    datalist=f.readlines()
    f.close()
    i=0
    for s in datalist:
        tmp = re.match(r'^(TATAMI_[A-z_0-9]+\s*[=].+)#',s)
        if tmp:
            exec('cfg.'+tmp.groups()[0])
        i=i+1
    set_config()
            
def save_config():
    ret = messagebox.askyesno('Write configuration','Write myconfig.py?')
    if not ret:return    
    f = open(fname)
    datalist=f.readlines()
    f.close()
    servo_max = servo_center.get()+servo_limit.get()
    servo_min = servo_center.get()-servo_limit.get()
    cfg.TATAMI_STEERING_LEFT_PWM = servo_max 
    cfg.TATAMI_STEERING_RIGHT_PWM = servo_min
    cfg.TATAMI_STEERING_FEEL=steering_feel.get()
    cfg.TATAMI_STEERING_BALANCE=steering_balance.get()
    cfg.TATAMI_THROTTLE_START_BOOST_TIME=throttle_start_boost_time.get()
    cfg.TATAMI_THROTTLE_START_BOOST=throttle_start_boost.get()
    cfg.TATAMI_THROTTLE_UPPER_LIMIT=throttle_upper_limit.get()
    cfg.TATAMI_THROTTLE_LOWER_LIMIT=throttle_lower_limit.get()
    cfg.TATAMI_THROTTLE_STEERING_BOOST=throttle_steering_boost.get()
    
    print('Write Parameter into:' + fname)
    i = 0
    for s in datalist:
        tmp = re.match(r'^(TATAMI_[A-z_0-9]+)\s*[=].+(#.+$)',s)
        if tmp:
            varname =tmp.groups()[0]
            val = str( eval('cfg.'+varname) )
            comment = tmp.groups()[1]
            d = varname+" = "+val+" "+comment
            datalist[i] = d+"\n"
            print(d)
        i = i + 1
    f=open(fname,'w')
    f.writelines(datalist)
    f.close()

def init_config():
    load_config()
    set_config()

def set_motor(motor_level):
    motor_v=int(motor_level)
    if motor_v > 0:
        pi.set_PWM_range(gpio_pin0, 100)  # Set PWM range
        pi.set_PWM_dutycycle(gpio_pin0,   motor_v) # Set PWM duty
        pi.set_PWM_frequency(gpio_pin0,490)
        pi.set_PWM_dutycycle(gpio_pin1,   0) # PWM off
    else:
        pi.set_PWM_range(gpio_pin1, 100)  # Set PWM range
        pi.set_PWM_dutycycle(gpio_pin1,   -motor_v) # Set PWM duty
        pi.set_PWM_frequency(gpio_pin1,490)
        pi.set_PWM_dutycycle(gpio_pin0,   0) # PWM off

def set_servo(x):
    servo_v = servo.get()
    servo_max = servo_center.get()+servo_limit.get()
    servo_min = servo_center.get()-servo_limit.get()
    if servo_limit_flag.get() and servo_v > servo_max:
        servo_v = servo_max
    elif servo_limit_flag.get() and servo_v < servo_min:
        servo_v = servo_min
    pi.set_mode(gpio_pin2, pigpio.OUTPUT)
    pi.set_servo_pulsewidth(gpio_pin2, servo_v )
    servo.set(servo_v)
    status()

def set_throttle(x):
    global throttle_start_boost_val
    th_in = throttle.get()
    throttle_abs = np.abs(th_in)
    
    #Steering Boost
    angle_adjust = throttle_lower_limit.get()+np.abs(steering.get())*(throttle_steering_boost.get()-throttle_lower_limit.get())

    #Feeling 
    if throttle_abs < throttle_lower_limit.get():
        throttle_feel = throttle_lower_limit.get()
    elif throttle_abs > throttle_upper_limit.get():
        throttle_feel = throttle_upper_limit.get()
    else:
        slope = throttle_upper_limit.get()-throttle_lower_limit.get()
        throttle_feel = throttle_lower_limit.get() + throttle_abs*slope
                          
    if throttle_abs > throttle_deadzone:
        if throttle_boost_enable_flag.get():
            th = np.sign(th_in)*max(throttle_start_boost_val,angle_adjust,throttle_feel)
        else:
            th = th_in
    else:
        th=0
    s1.set(th*100)
    
def set_steering(x):
    angle = steering.get()
    #Steering Feeling Adjustment
    ang_abs=np.abs(angle)
    steering_half=0.5
    if ang_abs < steering_half:
        slope = steering_feel.get()/steering_half
        angle = np.sign(angle)*ang_abs*slope
    else:
        slope = (1.0-steering_feel.get())/(1.0-steering_half)
        angle = np.sign(angle)* (steering_feel.get()+(ang_abs-steering_half)*slope)
            
    #Steering Balance Adjustment
    if angle>0:
        angle =  angle * (1.0+steering_balance.get())
    else:
        angle =  angle * (1.0-steering_balance.get())
            
    v = servo_center.get()-servo_limit.get()*angle
    s2.set(v)
    set_throttle(0)
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

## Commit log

2021-05-11 Add files via upload
    TatamiRacer Kit Ver 1.0
    [tatamiracer_assembly.stl, tatamiracer_kit.stl]
2022-05-15 Add files via upload
    Add connector exchange figure
2022-06-19 Add files via upload
    Encoder kit as optional parts
    [tatamiracer_encoder_kit.stl]
2022-06-19 Add files via upload
    Expand shaft hole size
    [tatamiracer_encoder_kit.stl]
2022-06-19 Add files via upload
    Change connector of camera cable
2022-10-08 Update README.md
    add pin headder
2022-10-08 Add files via upload
    new 6t pinion gear
    [pinion_gear_6t.stl]
2024-08-10 Add files via upload
    fixed motor 3d object
    [tatamiracer_assembly.stl]
2024-08-10 Add files via upload
    fixed motor 3d data
    [tatamiracer_assembly.stl]
2024-08-12 Add files via upload
    Small change of size of rear body stopper
    [tatamiracer_kit.stl]
2024-08-17 Add files via upload
    Improved servo hole position of holder parts
    [tatamiracer_assembly.stl, tatamiracer_kit.stl]
2024-10-14 Add Lidar
2024-10-14 Add files via upload
    - Increased depth of connection between front Raspberry Pi mount and camera mount
    - Improved contact between rear Raspberry Pi mount and encoder connector
    [tatamiracer_assembly.stl, tatamiracer_kit.stl]
2024-10-14 Add files via upload
    - Improved gear size and connector size
    [tatamiracer_encoder_kit.stl]
2024-10-16 Add files via upload
    Improved encoder size for detection stability
    [tatamiracer_encoder_kit.stl]
